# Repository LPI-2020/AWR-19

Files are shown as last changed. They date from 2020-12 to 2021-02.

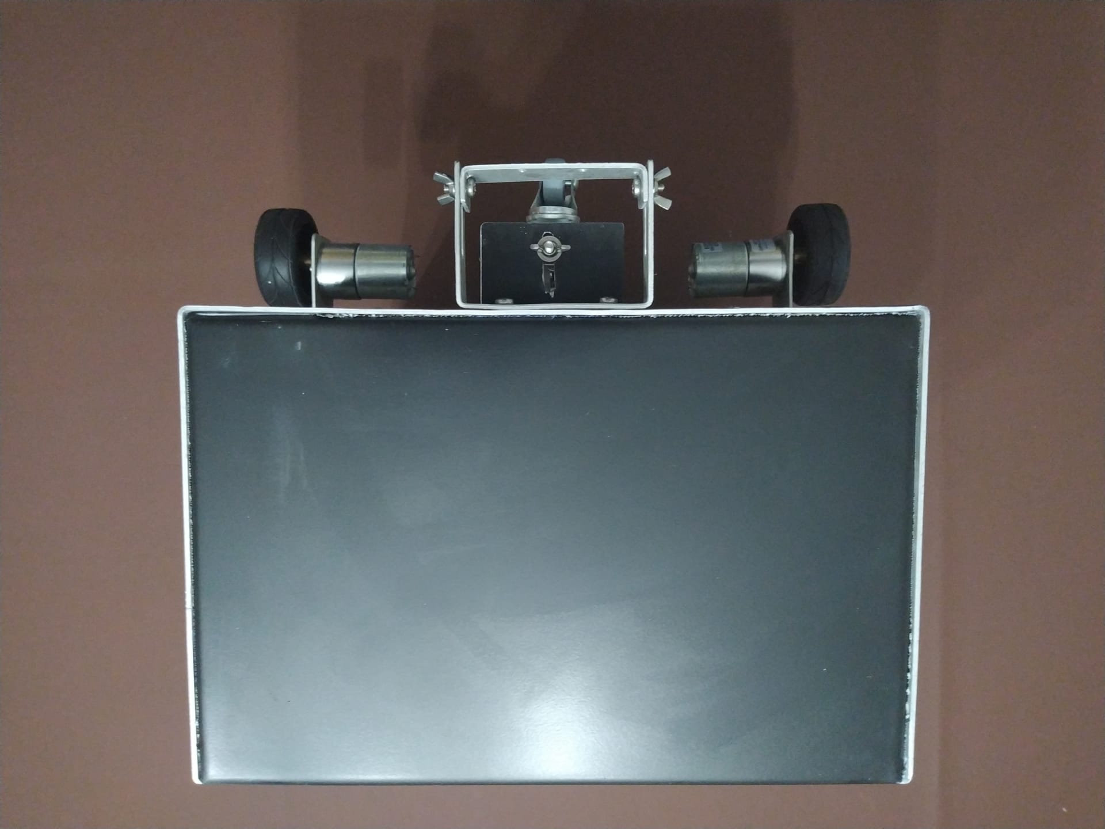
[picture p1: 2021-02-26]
01Relatorios/Images/FotosRobo/frente.jpg

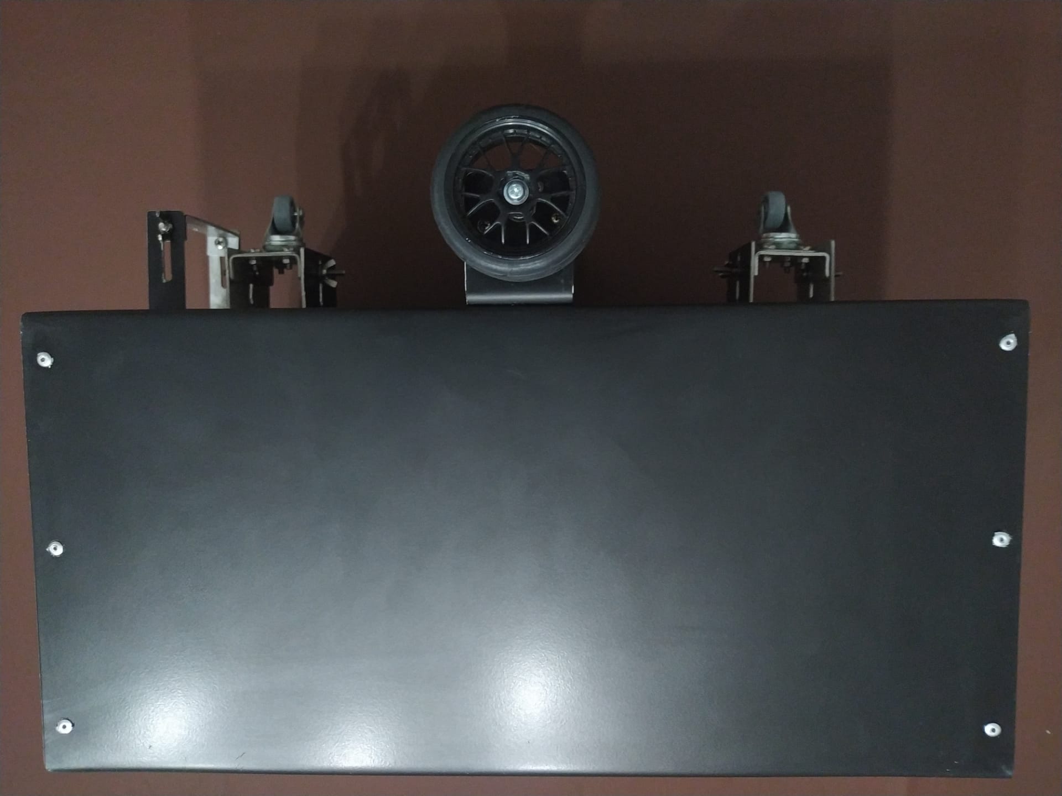
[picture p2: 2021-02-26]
01Relatorios/Images/FotosRobo/lado_esq.jpg

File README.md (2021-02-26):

# Analog Waiter Robot (AWR-19)

Developed in:
- Projeto Integrador - LPI I (2020)

Members:
- Bruno Miguel Vasconcelos da Silva, a88289
- Diogo Miguel Cunha Fernandes, a88262
- Duarte Miguel Novo Rodrigues, a88259
- Francisco Lopes Salgado, a88231 
- João Pedro Dias Miranda, a88237
- José Tomás Lima de Abreu, a88218

Directed by:
- Luís Barros

Short description (PT):
- O Analog Waiter Robot (AWR) é um robô seguidor de linha focado na assistência a pessoas em isolamento que não podem contactar com o mundo exterior. Basta colocar no seu suporte o que pretende fazer chegar ao paciente, colocá-lo sobre a linha, ligá-lo e este seguirá o percurso até ao destino.

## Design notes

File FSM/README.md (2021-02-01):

# PI-LPI_I/FSM

**_Version_ currently in use: v1.8**

Resources - Holds various materials that helped or will help implement features.

v1 - Robot makes 180 degree turn when arriving at the end of the line and then stops.
     After that, whenever the user wants to send back the robot, a button can be pressed to begin movement.

v2 - Robot stops at the end of the line. After that, whenever the user wants to send back the robot,
     a button can be pressed to begin movement in the opposite direction that he came.

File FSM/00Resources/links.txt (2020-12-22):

Driver Motores: https://www.botnroll.com/pt/motores-e-atuadores/1000-l298n-motor-driver-board-.html
Toggle: https://www.allaboutcircuits.com/technical-articles/t-is-for-toggle-understanding-the-t-flip-flop/
Mapa karnough: http://www.32x8.com/var6.html
Debounce: https://www.youtube.com/watch?v=tmjuLtiAsc0

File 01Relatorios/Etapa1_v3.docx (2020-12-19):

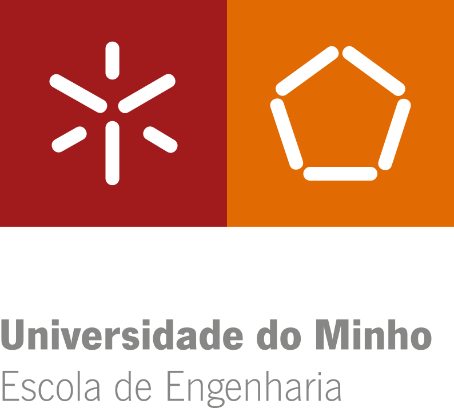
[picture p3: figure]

Bruno Miguel Vasconcelos da Silva, a88289

Diogo Miguel Cunha Fernandes, a88262

Duarte Miguel Novo Rodrigues, a88259

Francisco Lopes Salgado, a88231

João Pedro Dias Miranda, a88237

José Tomás Lima de Abreu, a88218

AWR-19

Analog Waiter Robot

Projeto integrador

Laboratórios e Práticas Integradas

Trabalho realizado sob a orientação do

Professor Luís Barros

dezembro de 2020

Índice

# Lista de Figuras

# Lista de Tabelas

# Acrónimos e Siglas

Acrónimo/Sigla | Significado
AWR LED | Analog Waiter Robot Light emitting diode

# Introdução

## Introdução

Perante o atual panorama pandémico da Covid-19 [1], pretende-se implementar uma ideia que terá um impacto positivo na vida das pessoas infetadas pela doença bem como dos que as rodeiam.

A maioria das ideias nesta área tem como foco principal a saúde pública da população em geral, tais como, robôs de desinfeção, por exemplo. Há menos projetos com foco individual em pessoas que tenham contraído a doença.

Na China existe um robô (little peanut) [2] com a mesma finalidade que foi utilizada num hotel para entregar comida porta a porta a hóspedes com suspeita de infeção.

Tendo em consideração que uma pessoa em isolamento deve evitar o contacto com o mundo exterior, pretende-se desenvolver um produto que permita a entrega e recolha de bens essenciais de forma segura. De forma a facilitar a sua desinfeção e o seu manuseamento, o robô deverá ter superfícies lisas e uma interface simples.

## Enquadramento

O Analog Waiter Robot (AWR) é um robô seguidor de linha focado na assistência a pessoas em isolamento que não podem contactar com o mundo exterior. Basta colocar no seu suporte o que pretende fazer chegar ao paciente, colocá-lo sobre a linha, ligá-lo e este seguirá o percurso até ao destino.

## Especificações previstas

O AWR terá de deslocar-se entre dois pontos, previamente definidos, com base numa linha instalada nos meios de acesso à divisão em que o paciente em questão se situa.

O AWR terá de ser colocado sobre a linha com os bens essenciais (comida e/ou alimentos) num tabuleiro. Após estar alinhado, deverá ser ligado por um funcionário responsável, para que inicie a sua trajetória. Ao chegar ao destino, demarcado com uma cruz no fim da linha, o robô terá de parar de forma a que o paciente recolha os bens a si destinados. Quando o paciente desejar, poderá acionar o robô de forma a que este reinicie o seguimento da linha de volta ao ponto de partida. Para tal, o AWR fará uma rotação de 180 ° sobre a linha e iniciar a marcha até ao ponto de início. Como a alimentação do robô será a baterias, eventualmente, terá de ser ligado à rede elétrica para ser carregado.

O tipo de desenvolvimento do nosso produto pode ser classificado como “misto”, uma vez que não tem necessariamente características inovadoras, mas é concebido para servir as necessidades particulares de um comprador. O produto será composto na sua totalidade por componentes ou subsistemas que são comprados “off-the-shelf”. Isto é, que só precisam de ser instalados e configurados para entrarem em funcionamento.

## Testes previstos

De forma a testar as especificações acima previstas, deverão ser realizados testes.

Para que o AWR siga a linha, será implementado um seguidor de linha através de um array de sensores de reflexão de luz. Irão ser realizados ensaios experimentais simulando o ambiente no qual este irá operar. Estes permitirão determinar os valores de referência que servirão para o dimensionamento e calibração dos circuitos de direção do robô. Para isso, este deverá ser colocado em diferentes posições sobre a linha.

Depois de determinados os valores de referência, deverão ser testados os circuitos de direção do robô, que usarão controladores para manter os valores dos sensores na gama de referência. Para isso, o AWR deverá ser colocado em diferentes posições sobre a linha para verificar se o controlador cumpre o seu propósito. Isto é, se o robô segue a linha até ao destino final.

Para controlar os diferentes estados de funcionamento do robô, irá ser desenvolvida uma máquina de estados baseada em circuitos sequenciais. De forma a testar o seu funcionamento, esta deverá ser sujeita a diferentes inputs de forma a verificar a comutação entre estados com a utilização de LEDs nas suas saídas. As saídas da máquina de estados irão controlar o estado de funcionamento dos motores.

Consoante as saídas da máquina de estados, cada motor poderá ter três modos de funcionamento: sentido horário, sentido anti-horário ou parado. Nesse momento poderão ser testadas todas as funcionalidades do robô, verificando se segue a linha ou não.

## Planeamento inicial

De forma a testar as especificações acima previstas, deverão ser realizados testes.

Para que o AWR siga a linha, será implementado um seguidor de linha através de um array de sensores de reflexão de luz. Irão ser realizados ensaios experimentais simulando o ambiente no qual este irá operar. Estes permitirão determinar os valores de referência que servirão para o dimensionamento e calibração dos circuitos de direção do robô. Para isso, este deverá ser colocado em diferentes posições sobre a linha.

Depois de determinados os valores de referência, deverão ser testados os circuitos de direção do robô, que usarão controladores para manter os valores dos sensores na gama de referência. Para isso, o AWR deverá ser colocado em diferentes posições sobre a linha para verificar se o controlador cumpre o seu propósito. Isto é, se o robô segue a linha até ao destino final.

Para controlar os diferentes estados de funcionamento do robô, irá ser desenvolvida uma máquina de estados baseada em circuitos sequenciais. De forma a testar o seu funcionamento, esta deverá ser sujeita a diferentes inputs de forma a verificar a comutação entre estados com a utilização de LEDs nas suas saídas. As saídas da máquina de estados irão controlar o estado de funcionamento dos motores.

Consoante as saídas da máquina de estados, cada motor poderá ter três modos de funcionamento: sentido horário, sentido anti-horário ou parado. Nesse momento poderão ser testadas todas as funcionalidades do robô, verificando se segue a linha ou não.

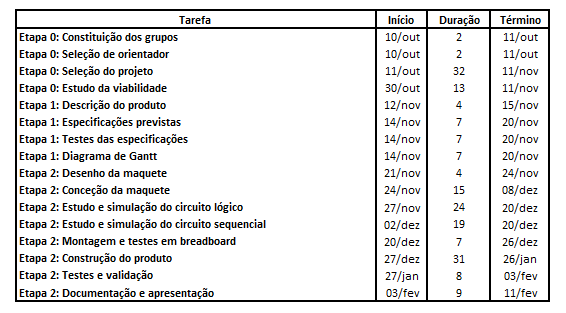
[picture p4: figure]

Tabela 1 - Planeamento do Projeto

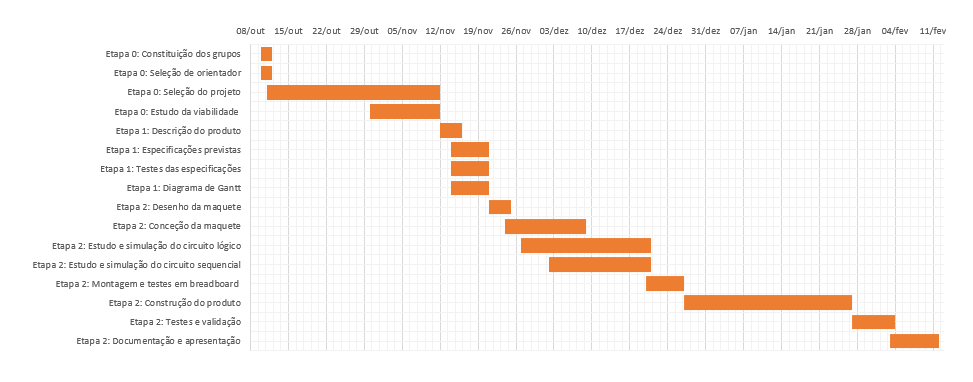
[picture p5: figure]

Figura 1 - Diagrama de Gantt

# Referências

[1] SNS - Serviço Nacional de Saúde, “Covid-19 | Pandemia,” 11 março 2020. [Online]. Available: https://www.sns.gov.pt/noticias/2020/03/11/covid-19-pandemia/. [Acedido em 16 dezembro 2020].

[2] J. D'Onfro, “Robots To The Rescue: How High-Tech Machines Are Being Used To Contain The Wuhan Coronavirus,” 2 fevereiro 2020. [Online]. Available: https://www.forbes.com/sites/jilliandonfro/2020/02/02/robots-to-the-rescue-how-high-tech-machines-are-being-used-to-contain-the-wuhan-coronavirus/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. [Acedido em 16 dezembro 2020].

LPI I | Projeto Integrador | AWR-19 xv Universidade do Minho

Lista de Figuras

Lista de Tabelas

Acrónimos e Siglas

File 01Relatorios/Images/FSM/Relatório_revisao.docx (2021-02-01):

3.3 - Sistema eletrónico para o controlo dos motores (pcbs e ligações)

De forma a ser possível controlar o estado de funcionamento do robô, ou seja, fazê-lo seguir a linha, parar ou rodar 180 °, desenvolveu-se uma máquina de estados sequencial síncrona, mais especificamente uma máquina de Moore, uma vez que as suas saídas dependem apenas do estado atual.

Figura 1 - Máquina de Moore

Numa máquina de estados, o objetivo é determinar a “Lógica do Próximo Estado” e a “Lógica de Saída” do circuito. Como referido, a “Lógica de saída” depende apenas do estado atual. Já a “Lógica do Próximo Estado” depende do estado atual e das entradas do circuito.

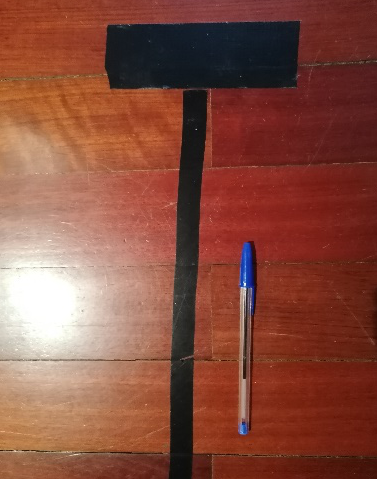
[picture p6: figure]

Como referido, o objetivo do robô é seguir uma linha, devendo parar sobre uma linha horizontal colocada no final do percurso (Figura 2) e, nesse momento, o robô deve dar uma volta de 180 ° sobre o seu eixo, voltando a seguir a linha em direção ao ponto de partida, após o acionamento de um botão.

Figura 2 - Linha preta usada para os testes

Denominou-se a linha de final de curso como a linha horizontal e a linha determinante do percurso como linha vertical.

De modo a detetar a linha no final do percurso, usaram-se os dois sensores das pontas do array de sensores (S1 e S8, rodeados a amarelo na Figura 4). Usou-se também o sensor do meio (S5, rodeado a verde na Figura 4) de forma a interromper a rotação quando este encontrar a linha preta.

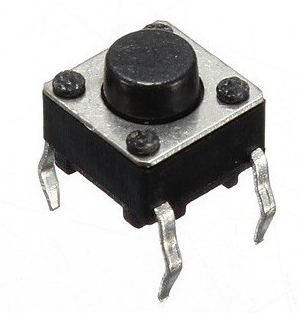
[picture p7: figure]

Nesse momento, o robô poderá ser acionado através de um botão de pressão (B) (Figura 3) para que este volte a seguir a linha.

Figura 3 - Botão de Pressão

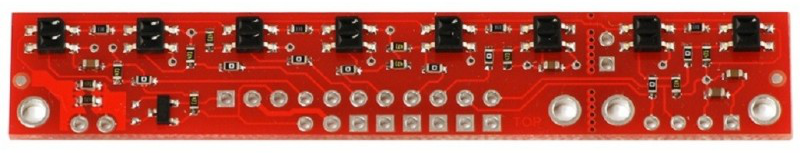
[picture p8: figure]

Figura 4 – Sensores usados na máquina de estados: S1, S5 e S8

Os motores são controlados por meio de um driver (L298N), podendo estar parados, a rodar no sentido horário ou no sentido anti-horário. O driver possui quatro entradas, duas por cada motor.

Para isso, na máquina de estados existem duas saídas por cada motor, sendo que uma controla o movimento no sentido horário e outra no sentido anti-horário.

Como o robô usa dois motores, existem quatro saídas, que quando estão ativas (nível lógico alto) despoletam as seguintes respostas:

- FWR – motor da direita roda no sentido horário;
- FWL – motor da esquerda roda no sentido horário;
- BWR – motor da direita roda no sentido anti-horário;
- BWL – motor da esquerda roda no sentido anti-horário.

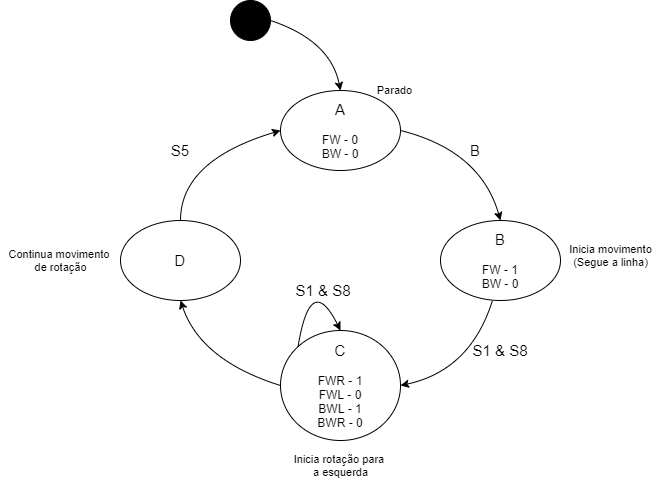
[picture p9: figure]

Na figura seguinte, mostra-se o diagrama da máquina de estados, usada para controlar o modo de funcionamento do robô. FW representa os valores de FWR e FWL e BW representa os valores de BWR e BWL.

Figura 5 - Diagrama da Máquina de Estados

Inicialmente, no estado “A”, o robô está parado (FW = 0 e BW = 0), e espera pelo acionamento do botão para iniciar a marcha. Após o acionamento do botão, B a nível lógico alto, no estado “B”, o robô inicia a sua trajetória, seguindo a linha com os dois motores a rodar no sentido horário (FW = 1 e BW = 0). Quando o array de sensores estiver posicionado sobre a linha horizontal preta (fim do trajeto), os sensores S1 e S8 estarão a nível lógico alto, e ocorrerá a transição para o estado “C”. Neste estado, o robô inicia a rotação para a esquerda (FWR = 1, FWL = 0, BWR = 0 e BWL = 1) e não transita de estado enquanto os sensores S1 e S8 estiverem a nível lógico alto, isto é, enquanto o array de sensores estiver sobre a linha horizontal. Quando o array de sensores sair desta, S1 e S8 estarão a nível lógico baixo, avançando para o estado “D”, no qual o robô continua a rotação, mantendo as suas saídas, até que o sensor S5 esteja sobre a linha vertical, S5 a nível lógico alto. Assim posicionado, o robô volta ao estado inicial.

Tabela 1 - Tabela Completa para Determinação da Lógica Completa da Máquina de Estados

De forma a implementar a máquina de estados, de acordo com o diagrama de estados, determinou-se toda a lógica necessária, construindo a tabela 1.

Adicionaram-se duas colunas que indicam os bits do estado atual (B1 e B0) e também as entradas da máquina de estados (S1, S5, S8 e B). Como existem quatro entradas, existem dezasseis (2⁴) combinações possíveis para cada estado, o que resulta em sessenta e quatro possibilidades no total (2⁴⁺² = 2⁶ = 64) que será o número de linhas da tabela 1.

A seguir, “E” representa o estado atual e “E*” o estado seguinte. “B1*” e “B0*” representam os bits do estado seguinte. Estas colunas devem ser preenchidas de acordo com a tabela ao lado (Tabela 2).

Tabela 2 - Atribuição de Estados

Sabendo que cada flip-flop permite a existência de dois estados e que existem quatro estados (A – D), selecionaram-se dois flip-flops do tipo J-K, que apresentam a tabela de excitação ao lado (Tabela 3). De acordo com esta tabela, foram preenchidas as colunas “J” e “K” para cada flip-flop (Ja e Ka, relativo a B0; Jb e Kb, relativo a B1). Para este efeito, determinou-se a lógica do próximo estado, em função das quatro entradas da máquina de estados, simplificada através de mapas de Karnaugh. Resolveram-se quatro mapas de Karnaugh (um para cada entrada J e K dos flip-flops) e obteve-se os resultados apresentados na figura 6.

Tabela 3 - Tabela de Excitação do Flip-Flop JK

Figura 6 - Lógica do Próximo Estado

Adicionaram-se as colunas das saídas (FWR, FWL, BWR e BWL), as quais foram preenchidas de acordo com o estado atual. Para cada uma destas determinou-se a lógica de saída, que também foi simplificada através de mapas de Karnaugh. Os resultados obtidos foram os da figura 7.

Figura 7 - Lógica de Saída

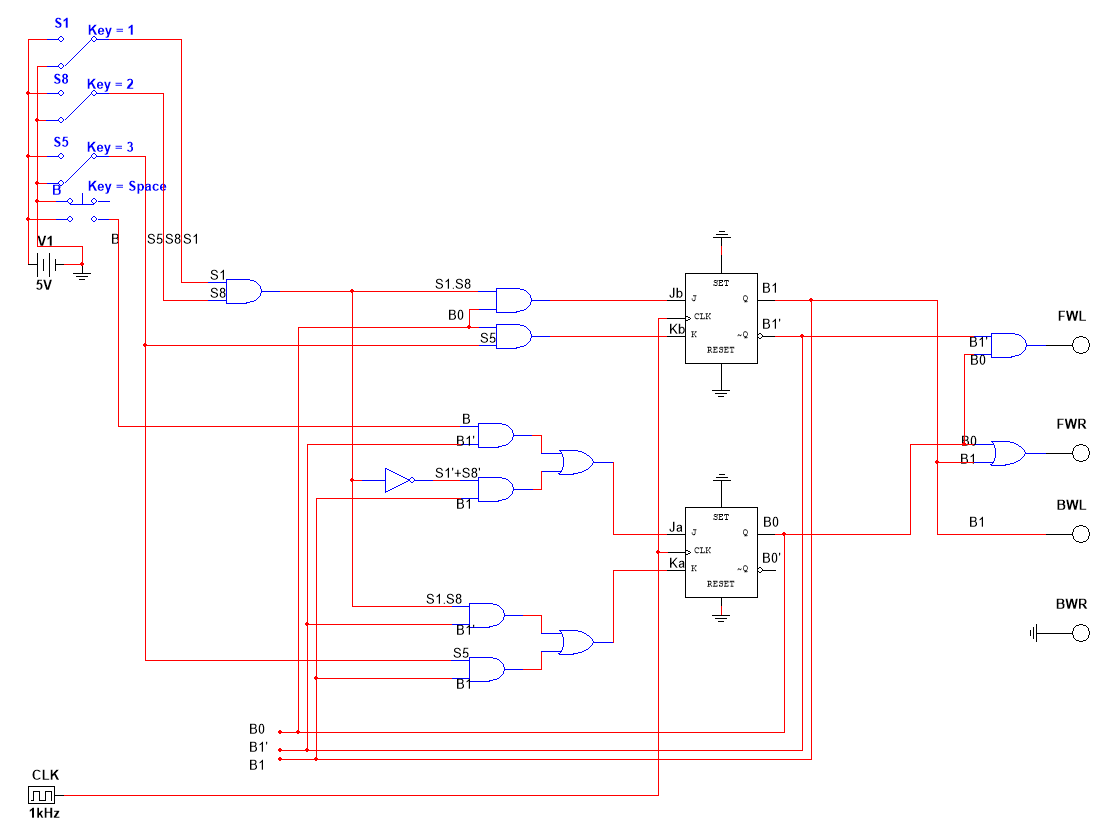
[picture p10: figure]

De acordo com a lógica determinada, desenhou-se o circuito que implementa a máquina de estados, o qual foi testado usando a ferramenta Multi-Sim, verificando-se a sua funcionalidade.

Lógica de próximo estado

Entradas

Figura 8 - Desenho da Máquina de Estados

Lógica de saída

Saídas

Flip-Flops

Estado atual

Lógica de Entrada

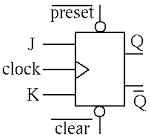
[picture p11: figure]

Tal como mostra a figura 9, cada Flip-Flop J-K necessita de um sinal clock como entrada. O clock é um sinal em forma de onda quadrada com um duty-cycle de, idealmente, 50 %. Dá-se uma transição entre estados sempre que, a cada pulso de clock, uma das entradas (J ou K) estiver a nível lógico alto.

Figura 9 - Esquema do Flip-Flop J-K

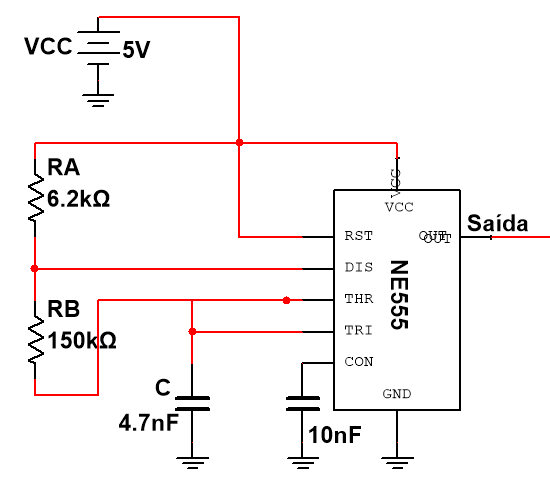
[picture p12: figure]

Para este efeito, implementou-se um oscilador usando o integrado NE555 numa montagem como multivibrador astável.

Figura 10 - Implementação do Oscilador

O condensador C1 carrega até 2*VCC/3 através das resistências RA e RB (saída = 1). Quando C1 atinge este valor, irá descarregar por RB (saída=0), até uma tensão de VCC/3 e o ciclo repete-se.

Para este efeito, implementou-se um oscilador usando o integrado NE555 numa montagem como multivibrador astável.

O condensador C1 carrega até 2*VCC/3 através das resistências RA e RB (saída = 1). Quando C1 atinge este valor, irá descarregar por RB (saída=0), até uma tensão de VCC/3 e o ciclo repete-se.

Através dos seguintes cálculos, dimensionaram-se os componentes para obter uma onda quadrada de frequência 1 kHz, duty-cycle de 50 %, aproximadamente.

T_(ON) =0,693 (RA+RB) C T_(OFF) =0,693 (RB) C

Duty-cyle=50 % ⇔T_(ON) = T_(OFF)

T= T_(ON) + T_(OFF) ⇔T=0,693 (R_A +2R_B ) C ⇔f= 1/T ⇔ f=(1,44)/((R_A +2R_B ) C) Para f=1 kHz e C=4,7 ηF :

(R_A + 2R_B )=306383

Duty-cyle=1- (R_B)/(R_A + 2R_B) ⇔R_B =0,5 (R_A + 2R_B ) ⇔R_B =0,5 ×306383 ⇔R_B =153,2 kΩ

(R_A + 2R_B )=306383

⇔R_A =6,4 kΩ

Foram selecionados os valores standard das resistências (Série E24) e do condensador (Série E12) mais próximos dos obtidos:

R_A =6,2 kΩ R_B =150 kΩ C=4,7 ηF

A figura 11 mostra a saída do circuito obtida em simulação com a ferramenta TINA.

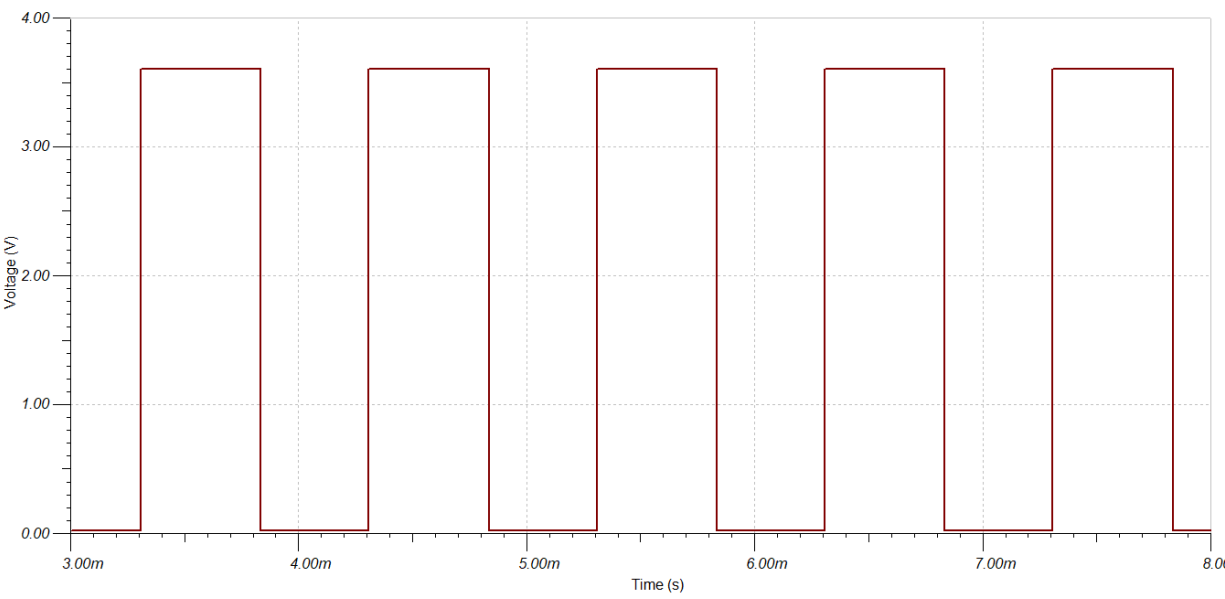
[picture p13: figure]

Figura 11 - Resposta do Oscilador de 1 kHz

As entradas Clear dos Flip-Flops J-K utilizados são ativas a nível lógico baixo, isto é, se ligarmos esta entrada ao ground, ocorrerá um reset no flip-flop e sua a saída Q virá a nível lógico baixo, independentemente das suas entradas J e K. Assim, se na máquina de estados as entradas Clear forem ligadas ao GND, B0 e B1 ficarão a nível lógico baixo.

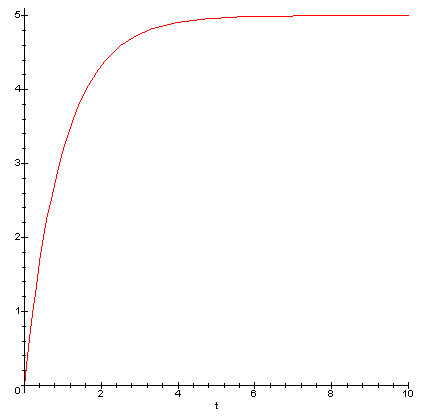
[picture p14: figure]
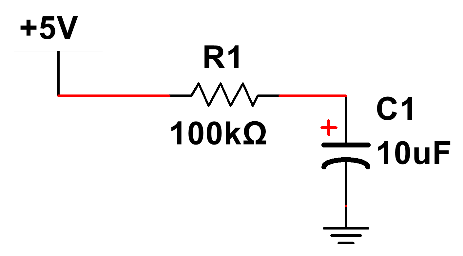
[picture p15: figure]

Experimentalmente, verificou-se que, quando alimentados, os flip-flops mantêm as saídas do estado anterior. Para que o robô inicie no primeiro estado de funcionamento (estado “A”), utilizou-se um circuito para efetuar um reset aos flip-flops, tal como mostra a figura 10.

Figura 12 - Circuito RC de Reset e a sua resposta no tempo.

Sabendo que a saída deste circuito estará a nível lógico baixo enquanto o condensador não carregar, a entrada reset dos flip-flops estará também a nível lógico baixo, o que resulta na ação de reset. Assim, logo que se alimentar a máquina de estados, os flip-flops apresentarão nas saídas “Q” o nível lógico baixo que representa o primeiro estado de funcionamento do robô. Após o condensador carregar, a entrada reset estará a nível lógico alto durante o resto do tempo de funcionamento, não provocando um reset indesejado.

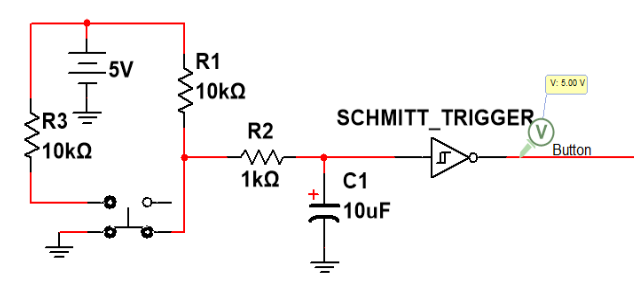
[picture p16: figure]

Foi usado um botão de pressão para que o robô inicie a marcha. No entanto, sabe-se que, quando uma saída provém diretamente de um botão de pressão, esta é afetada por problemas de vibração mecânica (bounce) quando o contacto se fecha. De forma a garantir que a mudança de nível lógico se faça sem oscilações, torna-se necessário implementar um circuito de debounce como, por exemplo, o apresentado na figura 13.

Figura 13 - Circuito de Debounce do Botão de Pressão (quando premido)

O condensador em conjunto com a resistência funciona como filtro passa-baixo, que ajuda a reduzir o ruído elétrico provocado pelas vibrações mecânicas do botão. Assim, quando o botão não está pressionado, os terminais do condensador apresentarão 5 V e, quando pressionado, apresentarão 0 V. Uma vez que, num circuito sequencial, o nível lógico alto corresponde ao acionamento de uma entrada (botão, neste caso), será necessário utilizar uma lógica inversora na saída do condensado. Para isso, usou-se uma porta lógica Schmitt-Trigger (integrado 74HCT14) que funciona como um circuito comparador inversor com histerese centrado em 0 V. Assim, aumenta a imunidade ao ruído e, como inverte, a saída do circuito estará a nível lógico alto quando o botão for pressionado.

Foi feito o teste em simulação do circuito da máquina de estados através da ferramenta Multi-Sim. Os resultados obtidos apresentam-se nas figuras abaixo. Verificou-se, portanto, a boa funcionalidade do circuito dimensionado.

Figura 14 - Estado 0 (Parado)

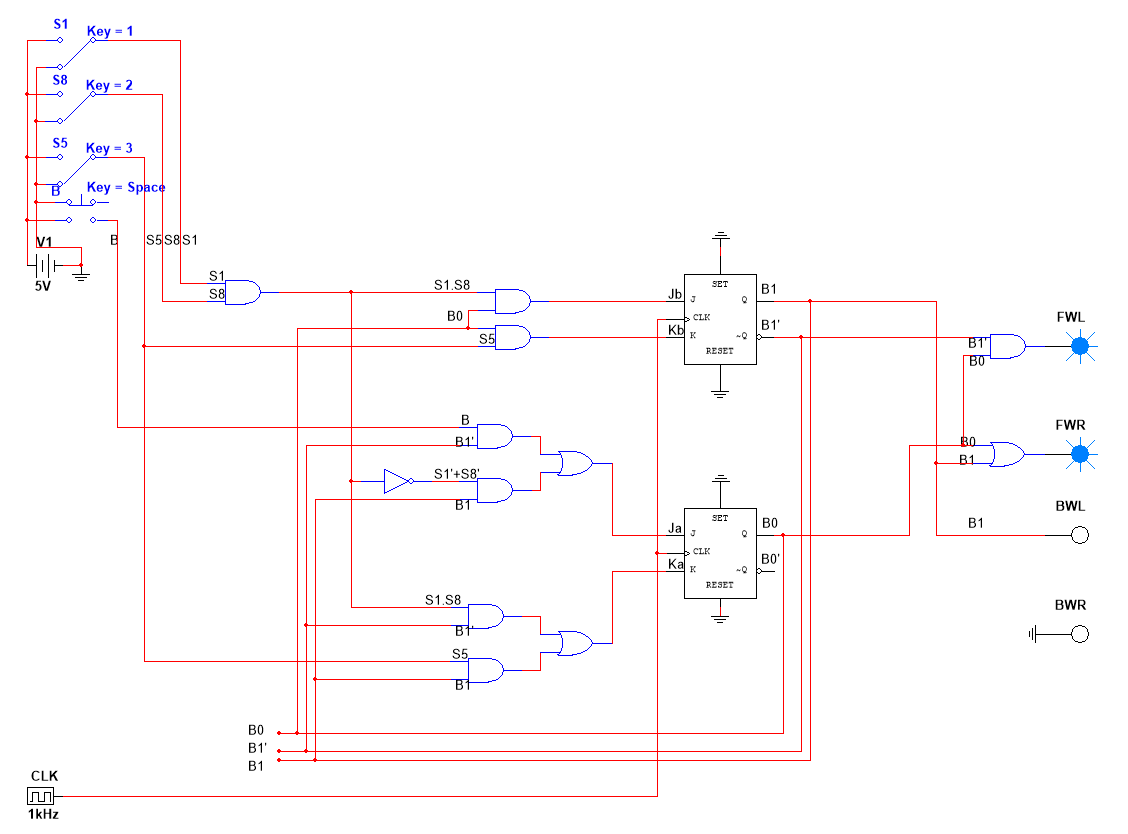
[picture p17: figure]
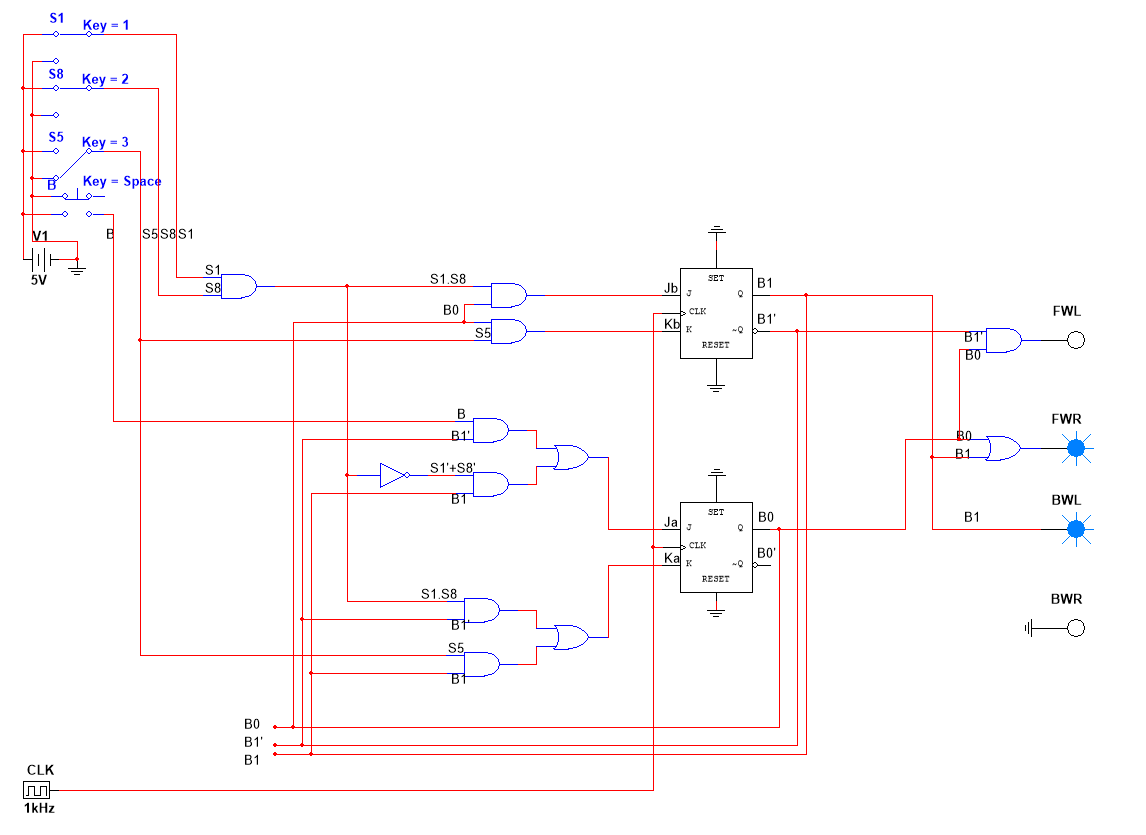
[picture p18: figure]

Figura 16 - Estado 1 (Anda para a frente) – Botão foi pressionado

Figura 15 - Estado 2 (Dá a volta para a esquerda) – S1 e S8 a nível lógico alto

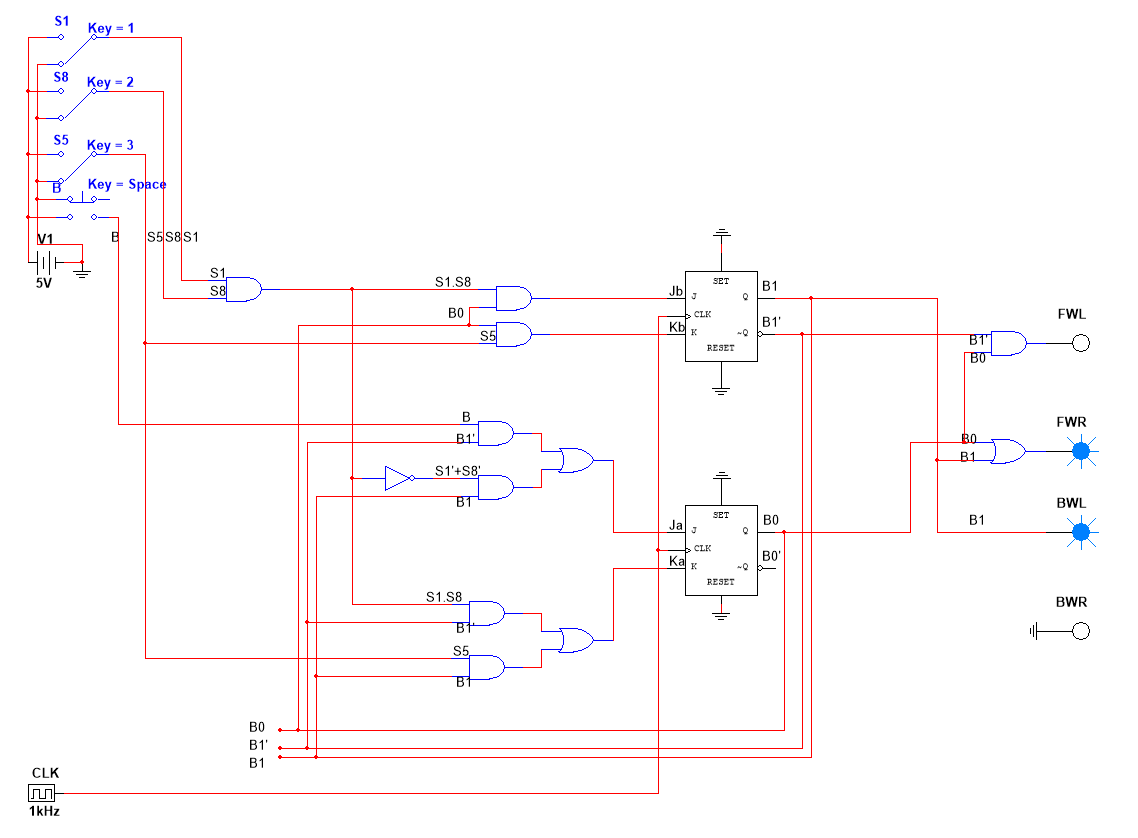
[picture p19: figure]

Figura 17 - Estado 3 (Dá a volta) - S1 e S8 a nível lógico baixo

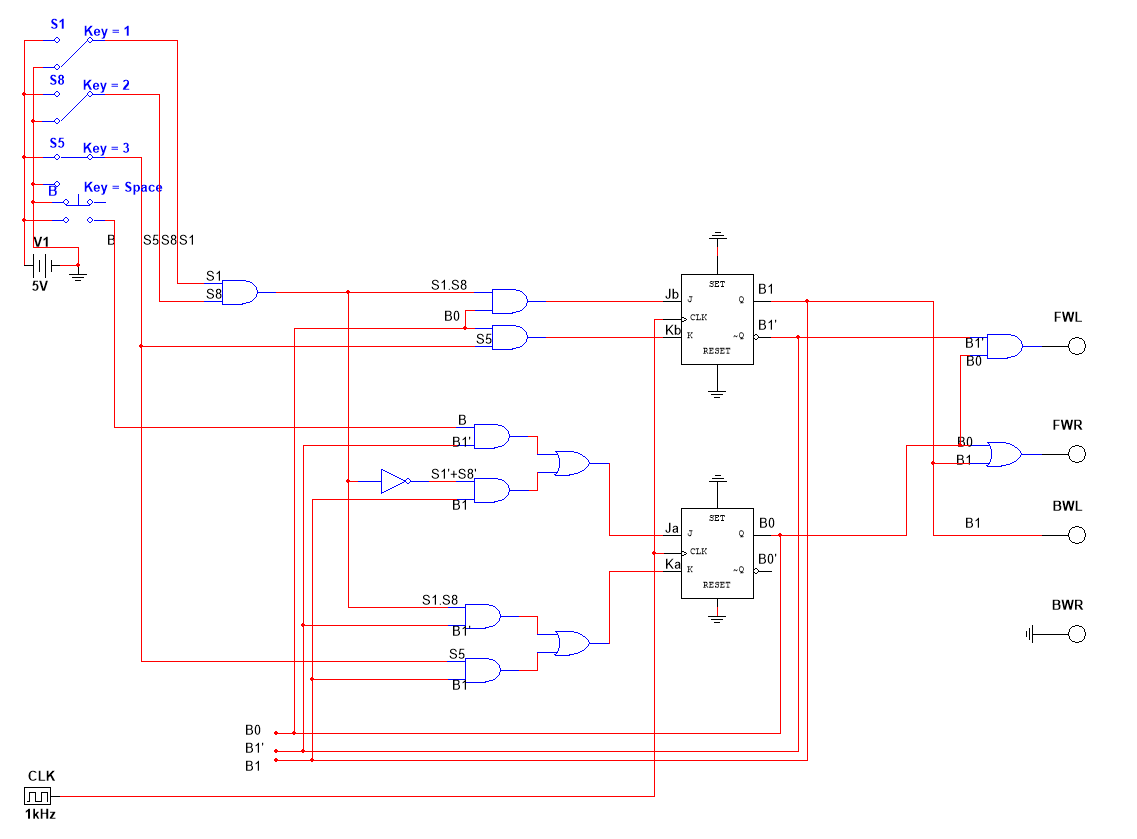
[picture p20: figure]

Figura 18 - Estado 0 (Parado novamente) - S5 = 1

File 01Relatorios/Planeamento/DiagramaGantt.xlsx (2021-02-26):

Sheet: 1a Versao
Tarefa | Início | Duração | Término
Etapa 0: Constituição dos grupos | 2020-10-10 | 2 | 2020-10-11
Etapa 0: Seleção de orientador | 2020-10-10 | 2 | 2020-10-11
Etapa 0: Seleção do projeto | 2020-10-11 | 32 | 2020-11-11
Etapa 0: Estudo da viabilidade | 2020-10-30 | 13 | 2020-11-11
Etapa 1: Descrição do produto | 2020-11-12 | 4 | 2020-11-15
Etapa 1: Especificações previstas | 2020-11-14 | 7 | 2020-11-20
Etapa 1: Testes das especificações | 2020-11-14 | 7 | 2020-11-20
Etapa 1: Diagrama de Gantt | 2020-11-14 | 7 | 2020-11-20
Etapa 2: Desenho da maquete | 2020-11-21 | 4 | 2020-11-24
Etapa 2: Conceção da maquete | 2020-11-24 | 15 | 2020-12-08
Etapa 2: Estudo e simulação do circuito lógico | 2020-11-27 | 24 | 2020-12-20
Etapa 2: Estudo e simulação do circuito sequencial | 2020-12-02 | 19 | 2020-12-20
Etapa 2: Montagem e testes em breadboard | 2020-12-20 | 7 | 2020-12-26
Etapa 2: Construção do produto | 2020-12-27 | 31 | 2021-01-26
Etapa 2: Testes e validação | 2021-01-27 | 8 | 2021-02-03
Etapa 2: Documentação e apresentação | 2021-02-03 | 9 | 2021-02-11

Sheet: 2a Versao
Tarefa | Início | Duração | Término
Etapa 0: Constituição dos grupos | 2020-10-10 | 1 | 2020-10-11
Etapa 0: Seleção de orientador | 2020-10-10 | 1 | 2020-10-11
Etapa 0: Seleção do projeto | 2020-10-11 | 31 | 2020-11-11
Etapa 0: Estudo da viabilidade | 2020-10-30 | 12 | 2020-11-11
Etapa 1: Descrição do produto | 2020-11-12 | 3 | 2020-11-15
Etapa 1: Especificações previstas | 2020-11-14 | 6 | 2020-11-20
Etapa 1: Testes das especificações | 2020-11-14 | 6 | 2020-11-20
Etapa 1: Diagrama de Gantt | 2020-11-14 | 6 | 2020-11-20
Etapa 2: Desenho da maquete | 2020-11-21 | 3 | 2020-11-24
Etapa 2: Conceção da maquete | 2020-11-24 | 14 | 2020-12-08
Etapa 2: Estudo e simulação do circuito lógico | 2020-11-27 | 23 | 2020-12-20
Etapa 2: Estudo e simulação do circuito sequencial | 2020-12-02 | 18 | 2020-12-20
Etapa 2: Montagem e testes em breadboard | 2020-12-20 | 33 | 2021-01-22
Etapa 2: Estudo de Fiabilidade, Certifiação e Segurança | 2021-01-23 | 18 | 2021-02-10
Etapa 2: Documentação e apresentação | 2021-01-23 | 19 | 2021-02-11

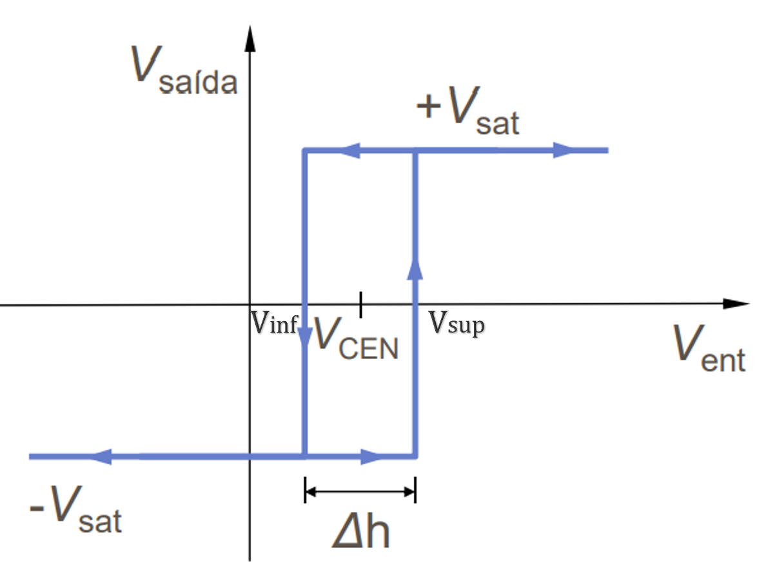
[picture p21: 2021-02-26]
01Relatorios/Images/histerese.png

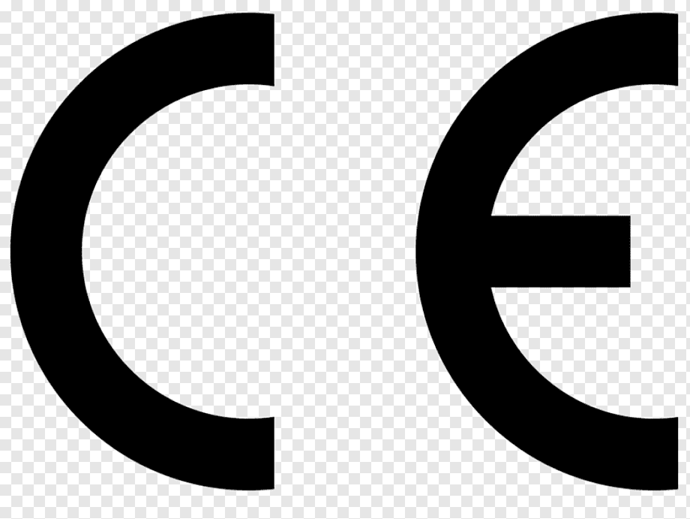
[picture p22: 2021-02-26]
01Relatorios/Images/Simbolos/ce.jpeg

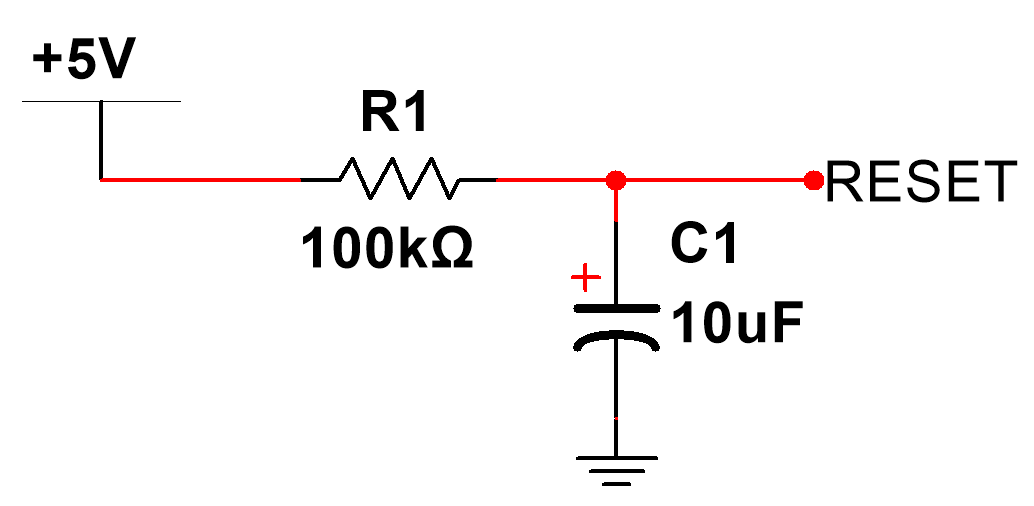
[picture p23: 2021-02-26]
01Relatorios/Images/FSM/circuitoRC.png

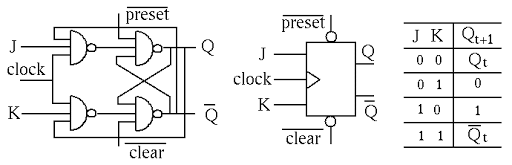
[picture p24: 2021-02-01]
01Relatorios/Images/FSM/FlipFlop_JK.png

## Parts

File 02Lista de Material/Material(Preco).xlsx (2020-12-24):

Material | Quantidade | Preço (€) (c/iva)
Motor Bot'n Roll ONE 300rpm | 2 | 35.001
Par de rodas Bot'n Roll ONE A | 1 | 11.500
Conjunto de Hubs para eixos 4mm c/exterior sextavado 12mm | 1 | 4.945
Rodas Livres | 2 | 3.000
Placa driver de motores L298N | 1 | 9.102
Suporte para uma pilha 18650 c/fios | 3 | 2.550
BMS para proteção Baterias 18650 3S 12,6V 20A | 1 | 3.948
Sensor QTR8A | 1 | 15
Circuitos Integrados | 10 | 10
Placa Impressa | 1
Acrilico | 1 | 0
Aluminio | 1 | 0
 |  | 95.046 | Total

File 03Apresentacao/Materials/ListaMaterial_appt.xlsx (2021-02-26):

 | Material | Quantidade | Preço unitário | Preço total
1 | Motores | 2 | 17.50 € | 35.00 €
2 | Rodas | 1 | 11.50 € | 11.50 €
3 | Par de hubs | 1 | 4.50 € | 4.50 €
4 | Rodas livres | 2 | 1.69 € | 3.38 €
5 | Módulo driver L298N | 1 | 12.90 € | 12.90 €
6 | QTR-8A | 1 | 19.90 € | 19.90 €
7 | Suporte pilha 18650 | 6 | 0.85 € | 5.10 €
8 | BMS | 2 | 5.50 € | 11.00 €
9 | Pilha LI-ION 18650 | 6 | 3.90 € | 23.40 €
10 | LM7805 | 1 | 0.50 € | 0.50 €
11 | TL494 | 2 | 1.70 € | 3.40 €
12 | LM324 | 2 | 1.95 € | 3.90 €
13 | LM358 | 5 | 0.74 € | 3.70 €
14 | 74HCT04 | 1 | 0.92 € | 0.92 €
15 | 74HCT08 | 2 | 0.90 € | 1.80 €
16 | 74HCT14 | 1 | 0.61 € | 0.61 €
17 | 74HCT32 | 1 | 0.48 € | 0.48 €
18 | 74HCT112 | 1 | 1.32 € | 1.32 €
19 | NE555P | 1 | 0.32 € | 0.32 €
20 | Terminal 2 pinos | 17 | 0.80 € | 13.60 €
21 | Terminal 3 pinos | 1 | 1.00 € | 1.00 €
22 | Potenciómetro | 2 | 2.20 € | 4.40 €
23 | Resistência | 34 | 0.05 € | 1.70 €
24 | Condensador cerâmico | 28 | 0.10 € | 2.80 €
25 | Condensador eletrolítico | 4 | 0.25 € | 1.00 €
26 | Botão de pressão | 2 | 0.15 € | 0.30 €
27 | Botão de painel | 1 | 0.60 € | 0.60 €
28 | Terminal 12 conetores | 3 | 0.40 € | 1.20 €
29 | Alumínio 2 mm | - | - | 35.00 €
30 | Placa madeira | 1 | - | 5.00 €
31 | Placa de acrílico policarbonato | 1 | - | 10.00 €
32 | Parafuso 5 mm | 28 | 0.05 € | 1.40 €
33 | Parafuso 3 mm | 12 | 0.05 € | 0.60 €
34 | Porca com asas 5 mm | 6 | 0.10 € | 0.60 €
35 | Porca 5 mm | 22 | 0.05 € | 1.10 €
36 | Rebites | 18 | 0.10 € | 1.80 €
37 | Anilhas | 12 | 0.01 € | 0.12 €
38 | Jumpers | pack | 2.00 € | 2.00 €
Total |  |  |  | 227.85 €

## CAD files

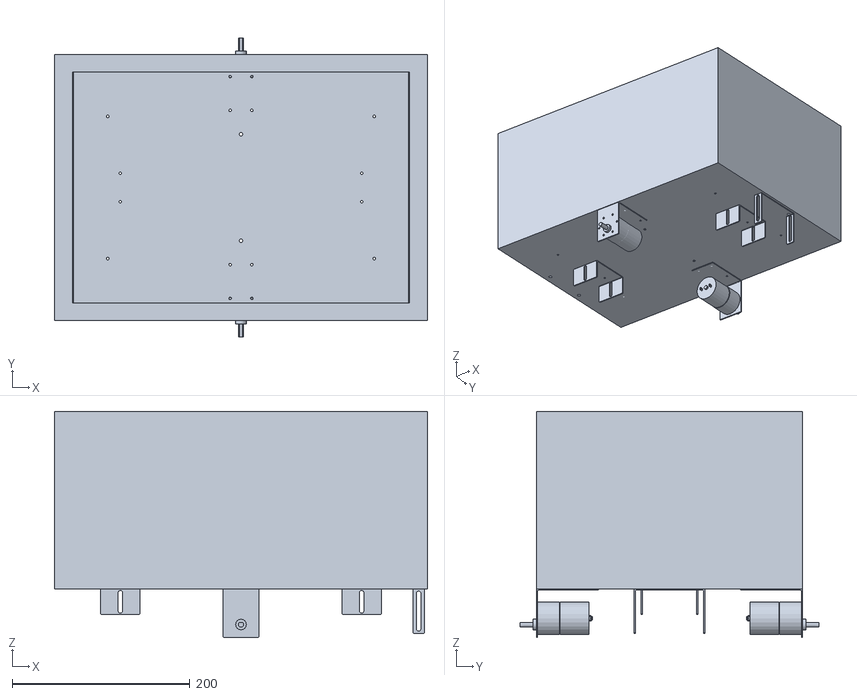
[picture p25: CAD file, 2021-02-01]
Diagramas/Model Robo v2.stl
420.0 x 337.0 x 255.0

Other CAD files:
Diagramas/Diagrama_Robo_v2.dwg

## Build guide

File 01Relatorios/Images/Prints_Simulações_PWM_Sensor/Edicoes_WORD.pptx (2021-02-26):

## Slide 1

1º Estágio

3º Estágio

4º Estágio

5º Estágio

2º Estágio

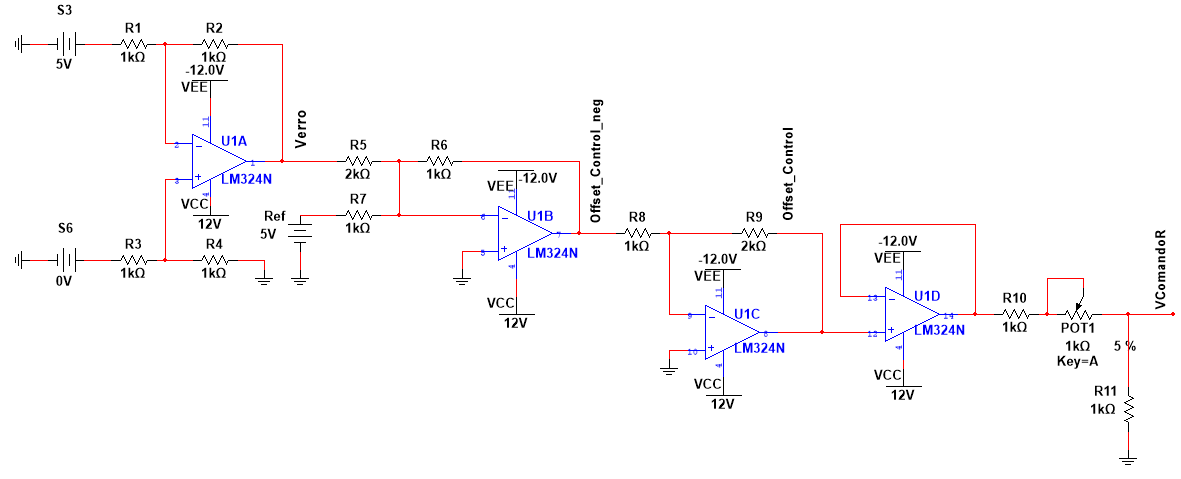
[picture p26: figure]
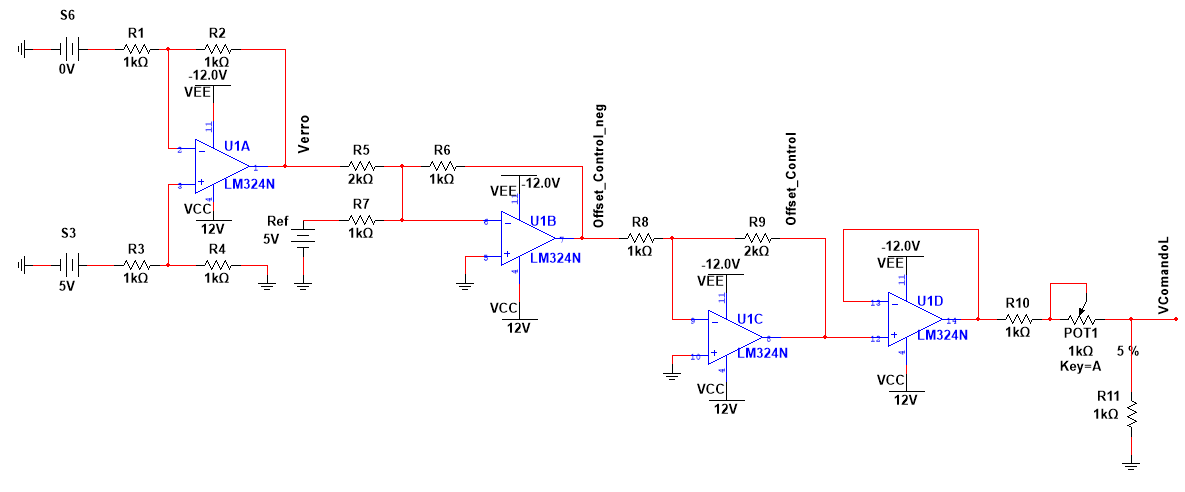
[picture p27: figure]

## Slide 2

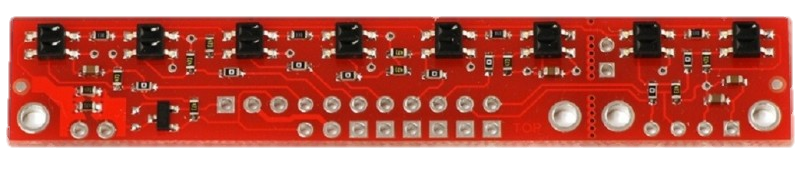
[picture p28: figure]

Sensor 1

Sensor 2

Sensor 3

Sensor 4

Sensor 5

Sensor 6

Sensor 7

Sensor 8

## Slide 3

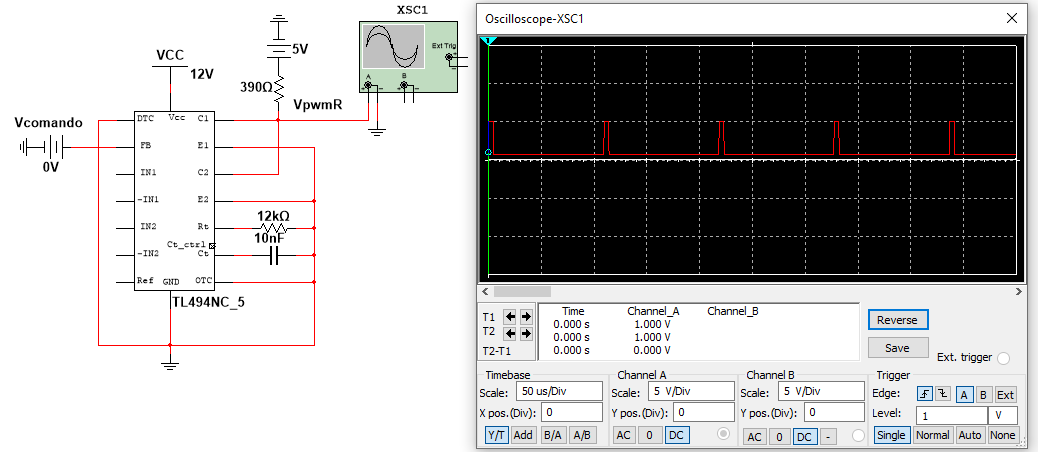
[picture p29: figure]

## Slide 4

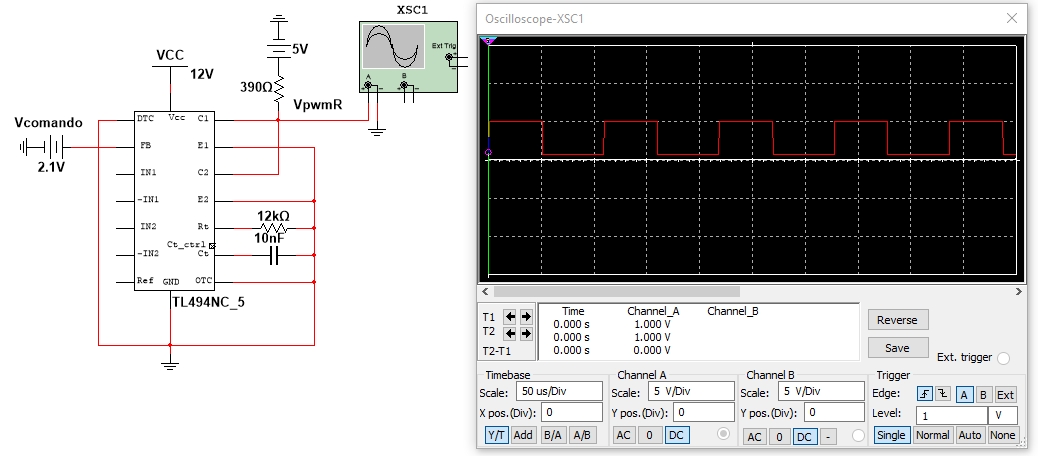
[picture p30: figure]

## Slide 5

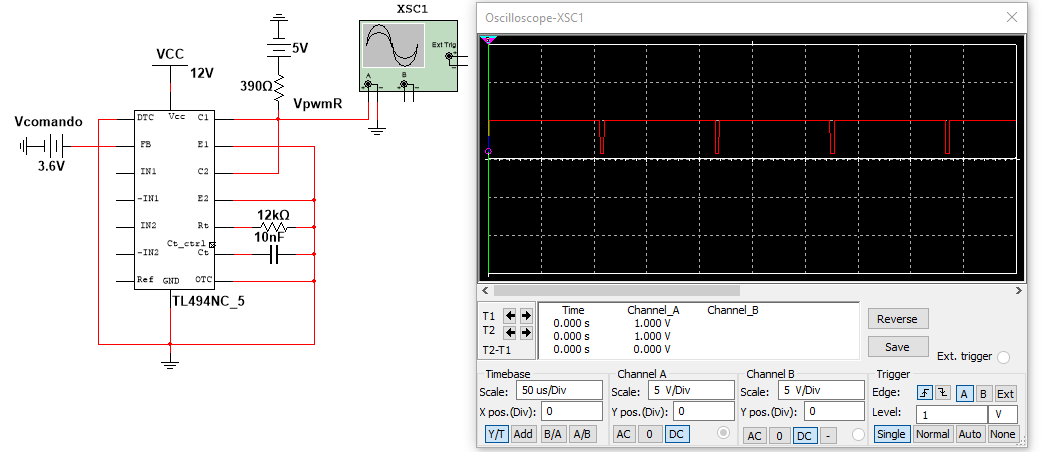
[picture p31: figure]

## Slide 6

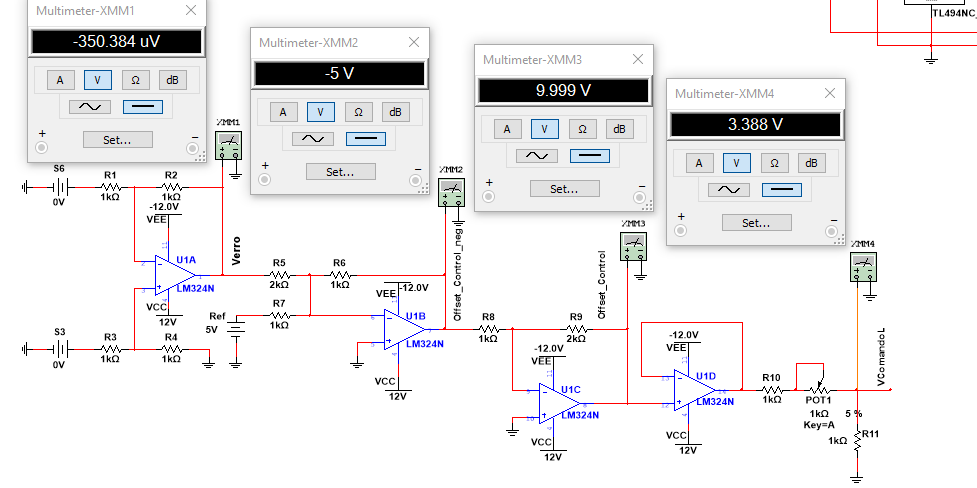
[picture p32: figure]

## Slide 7

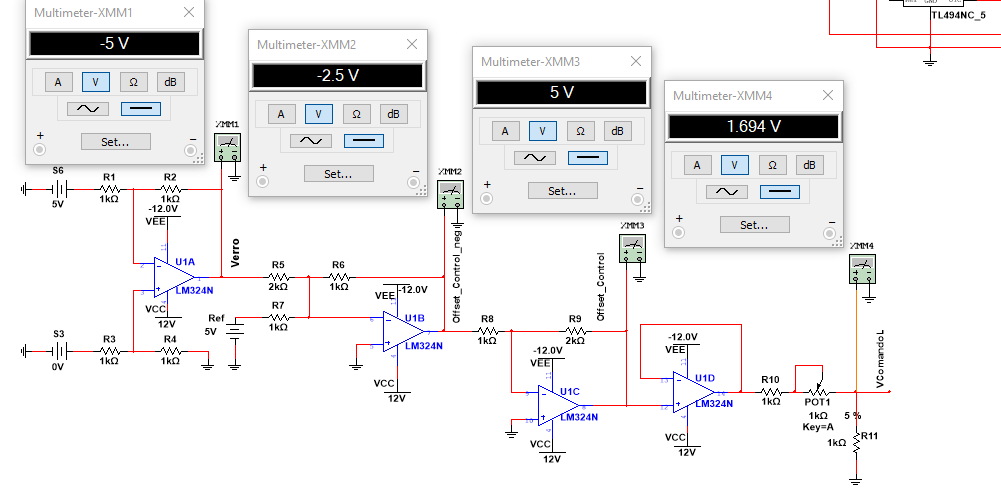
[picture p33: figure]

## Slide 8

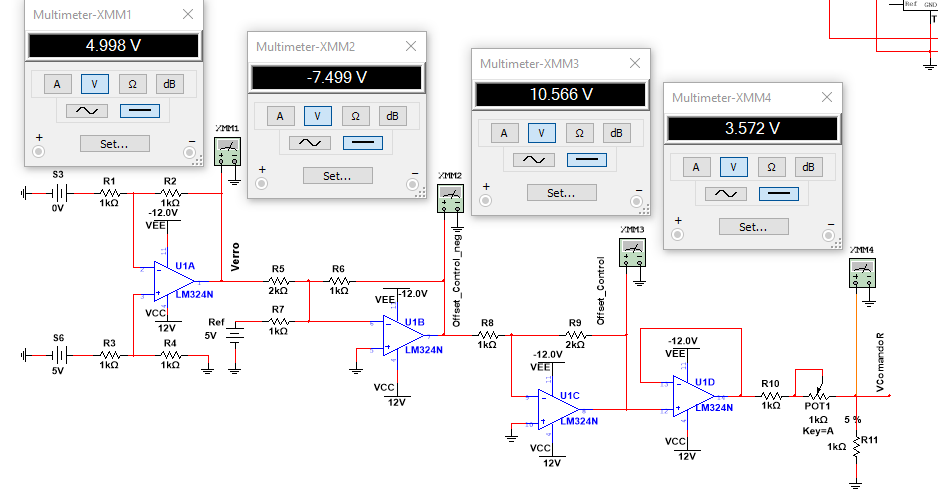
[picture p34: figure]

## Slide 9

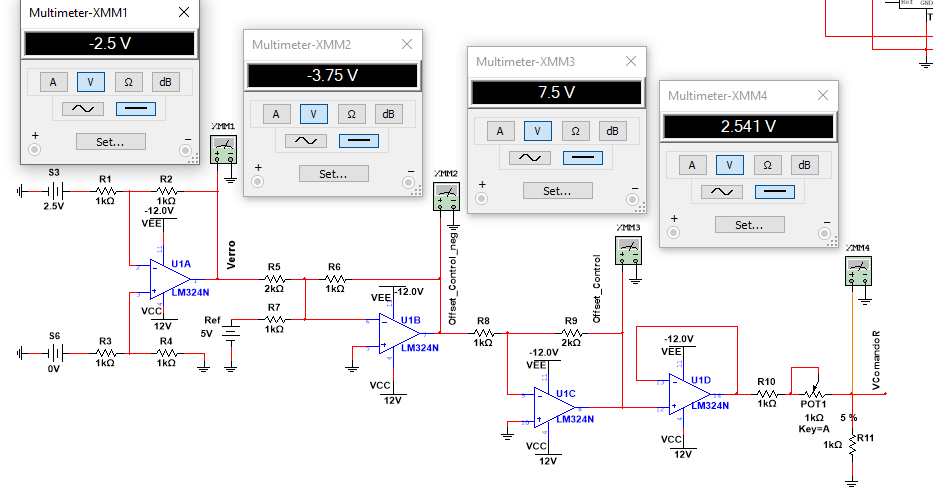
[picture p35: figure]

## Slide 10

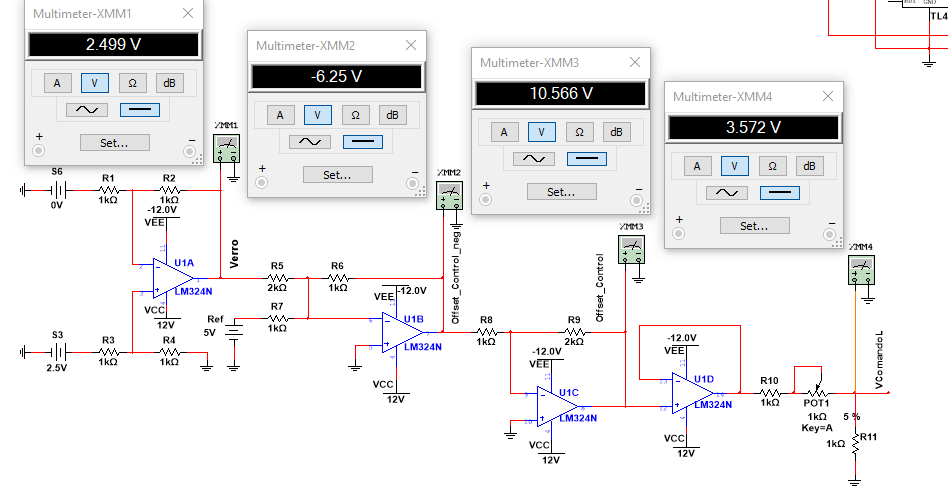
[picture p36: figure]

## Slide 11

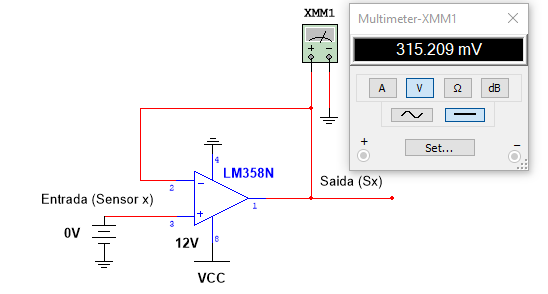
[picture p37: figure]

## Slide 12

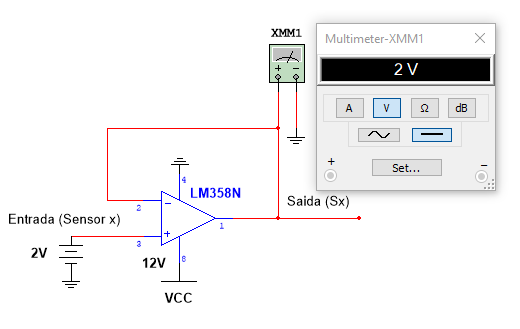
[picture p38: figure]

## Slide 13

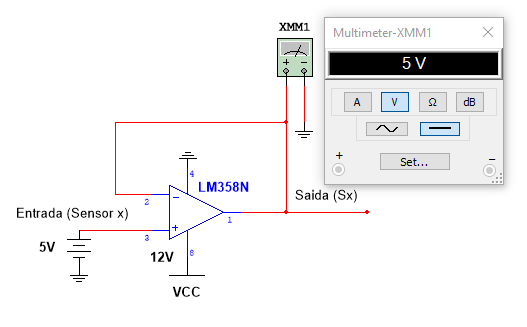
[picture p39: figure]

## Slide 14

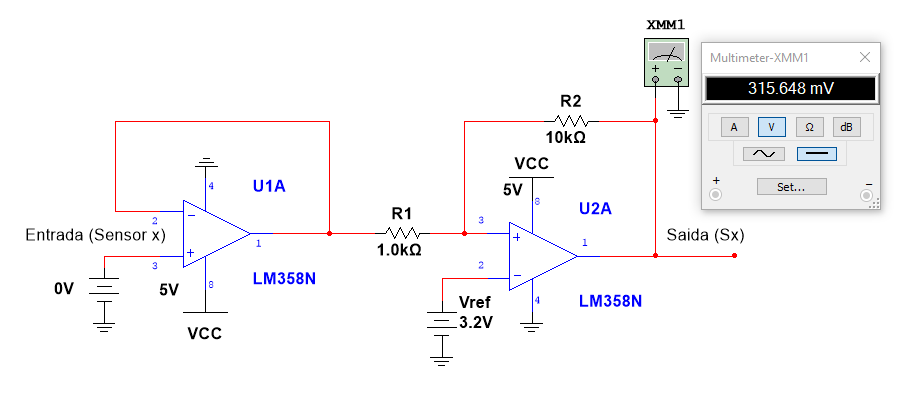
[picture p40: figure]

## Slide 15

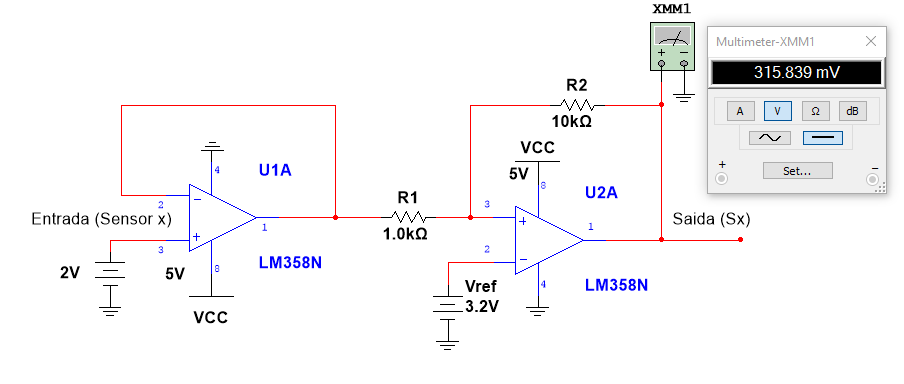
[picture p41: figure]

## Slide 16

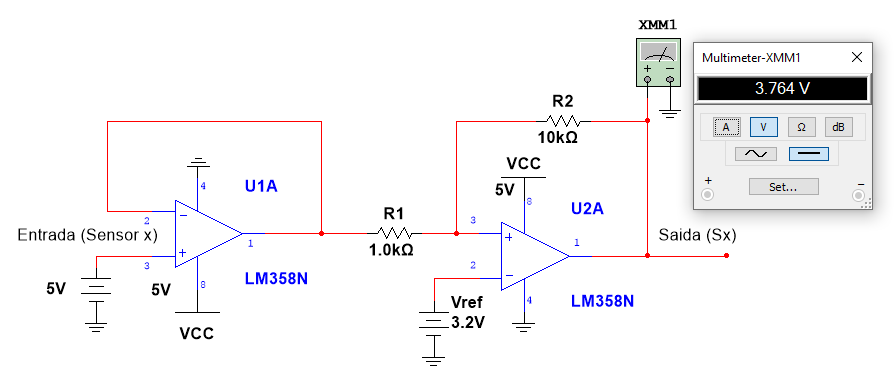
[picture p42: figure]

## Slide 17

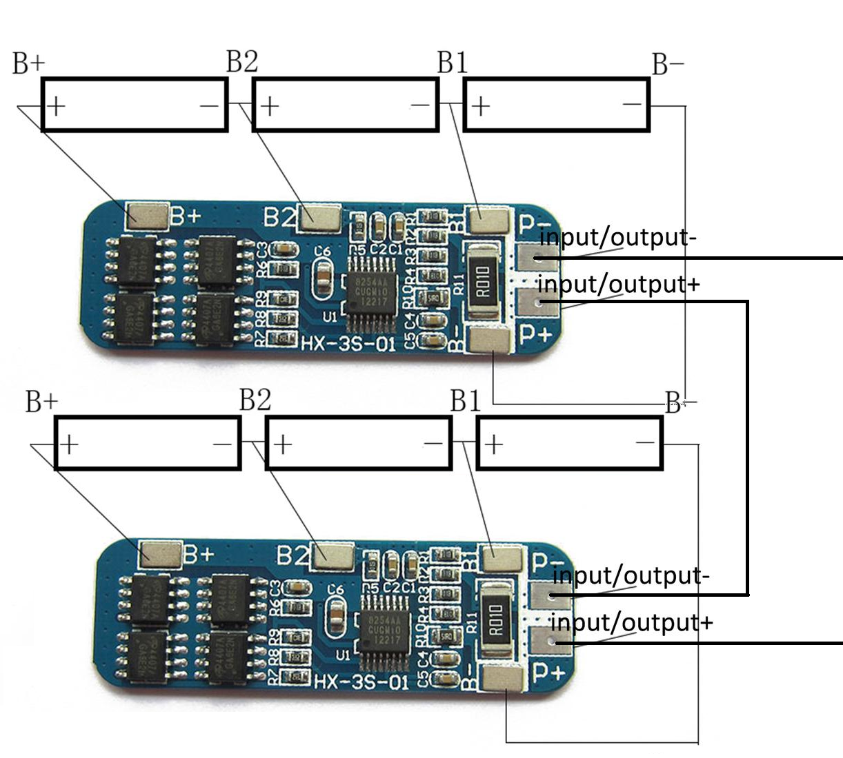
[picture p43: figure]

-12 V

GND

+12 V

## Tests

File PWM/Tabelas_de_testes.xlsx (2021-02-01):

verro | duty
1.15 | 0
1.39 | 10
1.9 | 30
2.3 | 50
2.9 | 70
3.35 | 90
3.6 | 100
vmedida | vref | ganho | verro |  | vmedida | vref | ganho | verro | vmedida | vref | ganho | verro | vmedida | vref | ganho | verro
0.5 | 4 | 1 | 3.5 |  | 0.5 | 5 | 1 | 4.5 | 0.5 | 4 | 4 | 14 | 0.5 | 4 | 1.2 | 4.2
1 | 4 | 1 | 3 |  | 1 | 5 | 1 | 4 | 1 | 4 | 4 | 12 | 1 | 4 | 1.2 | 3.6
1.5 | 4 | 1 | 2.5 |  | 1.5 | 5 | 1 | 3.5 | 1.5 | 4 | 4 | 10 | 1.5 | 4 | 1.2 | 3
2 | 4 | 1 | 2 |  | 2 | 5 | 1 | 3 | 2 | 4 | 4 | 8 | 2 | 4 | 1.2 | 2.4
2.5 | 4 | 1 | 1.5 |  | 2.5 | 5 | 1 | 2.5 | 2.5 | 4 | 4 | 6 | 2.5 | 4 | 1.2 | 1.8
3 | 4 | 1 | 1 |  | 3 | 5 | 1 | 2 | 3 | 4 | 4 | 4 | 3 | 4 | 1.2 | 1.2
3.5 | 4 | 1 | 0.5 |  | 3.5 | 5 | 1 | 1.5 | 3.5 | 4 | 4 | 2 | 3.5 | 4 | 1.2 | 0.6
4 | 4 | 1 | 0 |  | 4 | 5 | 1 | 1 | 4 | 4 | 4 | 0 | 4 | 4 | 1.2 | 0
4.5 | 4 | 1 | -0.5 |  | 4.5 | 5 | 1 | 0.5 | 4.5 | 4 | 4 | -2 | 4.5 | 4 | 1.2 | -0.6
 |  |  |  |  | vmedida | vref | ganho | verro | vmedida | vref | ganho | verro
 |  |  |  |  | 0.5 | 4.9 | 1.6 | 7.04 | 0.5 | 4.5 | 2.2 | 8.8
 |  |  |  |  | 1 | 4.9 | 1.6 | 6.24 | 1 | 4.5 | 2.2 | 7.7
 |  |  |  |  | 1.5 | 4.9 | 1.6 | 5.44 | 1.5 | 4.5 | 2.2 | 6.6
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

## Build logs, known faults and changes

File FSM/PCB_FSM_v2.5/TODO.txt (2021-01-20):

- A porta 74LS14 - Shmitt Trigger é usada na saída do circuito de debounce. Também deverá ser utilizada
para conectar as saídas dos sensores S1 e S8 à PCB da fsm, visto que esses valores poderão não ser exatamente
0 ou 5V, e a Shmitt Trigger compensa isso. Visto que cada 74LS14 tem 4 portas poderemos usar o IC apenas
nesta PCB. Depois só é necessário ligar os S1, S8 e B a um jumper.

- Verificar se quando é retirada a alimentação dos flip flops JK ocorre reset do estado. Ou seja,
verificar se ao ligar o robot após ter sido desligado enquanto estava em andamento, que B1 e B0
iniciam a 0, e não, com os valores dos últimos estados.
 
- Alterei a porta lógica que ligava ás ANDs de saída por uma OR, visto que (B1'&B0')' = B1+B0

- Ter em atenção que algumas entradas dos JK estão negadas. Temos portas NANDs já compradas, caso queiramos usar.
Além disso temos OR, AND, NOT, Shmitt Trigger, NAND, JK e NE555.

- Ter em atenção que vamos ter 4 jumpers de saída, para ligar ao Driver.

- Ver se vale a pena pôr LEDs para indicar o estado atual, em B0 e B1.

------------------- 02/01/2021 ------------------

- NE555: confirmar o IC; verificar se as portas deste IC são negadas (no PADS estão RES, THR e DIS).

- Dilema: Usar varios IC e menos ligações vs minimo de ICs e ligações mais complicadas.

- Verificar se foram usados os componentes corretos, tais como condensadores e resistencias.

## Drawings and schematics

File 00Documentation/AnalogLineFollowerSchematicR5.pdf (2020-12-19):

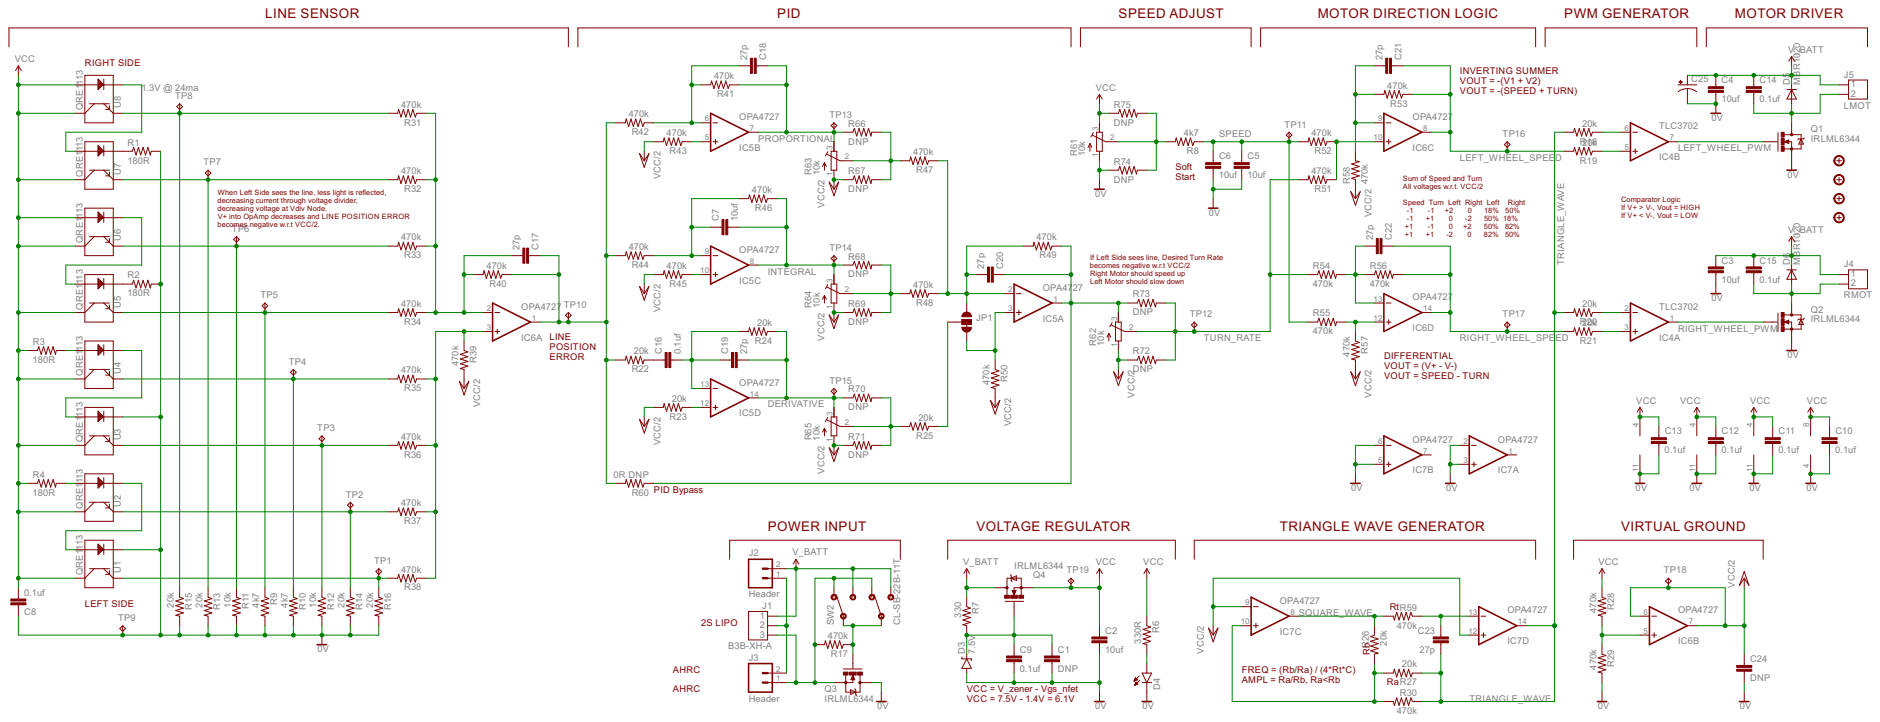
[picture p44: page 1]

INVERTING SUMMER
VOUT = -(V1 + V2) VOUT = -(SPEED + TURN)

When Left Side sees the line, less light is reflected, decreasing current through voltage divider, decreasing voltage at Vdiv Node. V+ into OpAmp decreases and LINE POSITION ERROR

If Left Side sees line, Desired Turn Rate
becomes negative w.r.t VCC/2 Right Motor should speed up

Left Motor should slow down

DIFFERENTIAL VOUT = (V+ - V-) VOUT = SPEED - TURN

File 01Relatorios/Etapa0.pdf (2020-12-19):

# AWR – 19

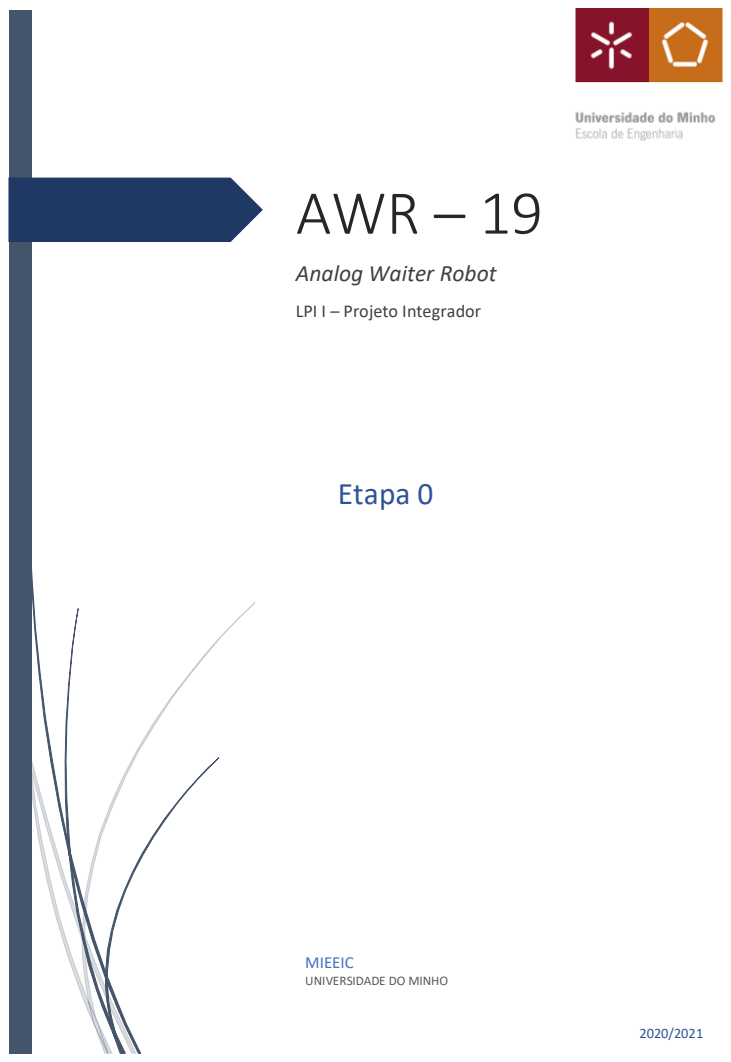
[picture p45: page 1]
Etapa 0

Analog Waiter Robot

LPI I – Projeto Integrador

MIEEIC
UNIVERSIDADE DO MINHO

1

### Grupo:

- Bruno Miguel Vasconcelos da Silva 88289
- Diogo Miguel Cunha Fernandes 88262
- Duarte Miguel Novo Rodrigues 88259
- Francisco Lopes Salgado 88231
- João Pedro Dias Miranda 88237
- José Tomás Lima de Abreu, 88218

### Coordenador / líder:

- João Pedro Dias Miranda 88237

### Orientador:

- Luís André Magalhães de Barros

### Nome do projeto:

- Analog Waiter Robot – 19 (AWR -19)

### Ideia do Produto:

A ideia do produto surgiu da necessidade de atuar perante o panorama pandémico (Covid-19), mais propriamente no auxílio a pessoas que se encontrem em isolamento.

Como todos sabemos, uma pessoa em isolamento não pode ter contacto com o mundo exterior. Por este motivo, pensámos em desenvolver um robô que faça chegar os bens essenciais à pessoa em isolamento.

A função principal do produto será desempenhar o papel de um “empregado de mesa”, daí o nome “Waiter”. O termo “Analog” advém do facto de todas funcionalidades serem implementadas de forma analógica, perfazendo o nome do robô “Analog Waiter Robot”.

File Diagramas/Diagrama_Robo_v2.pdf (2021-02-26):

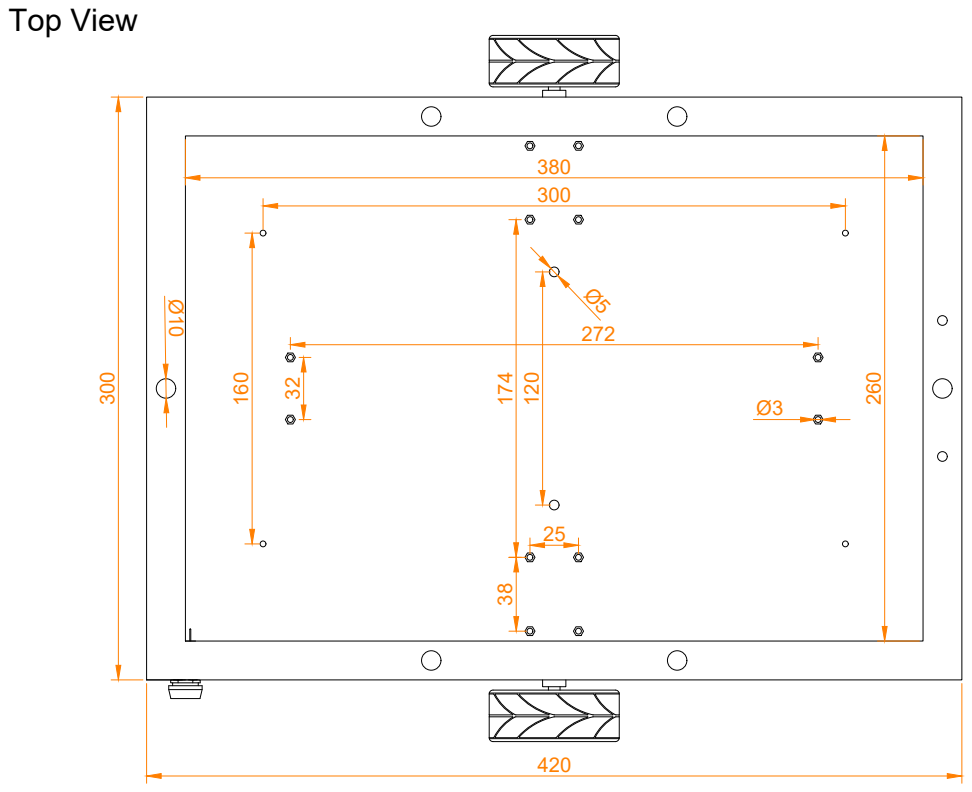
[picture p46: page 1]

260 Top View Bottom View

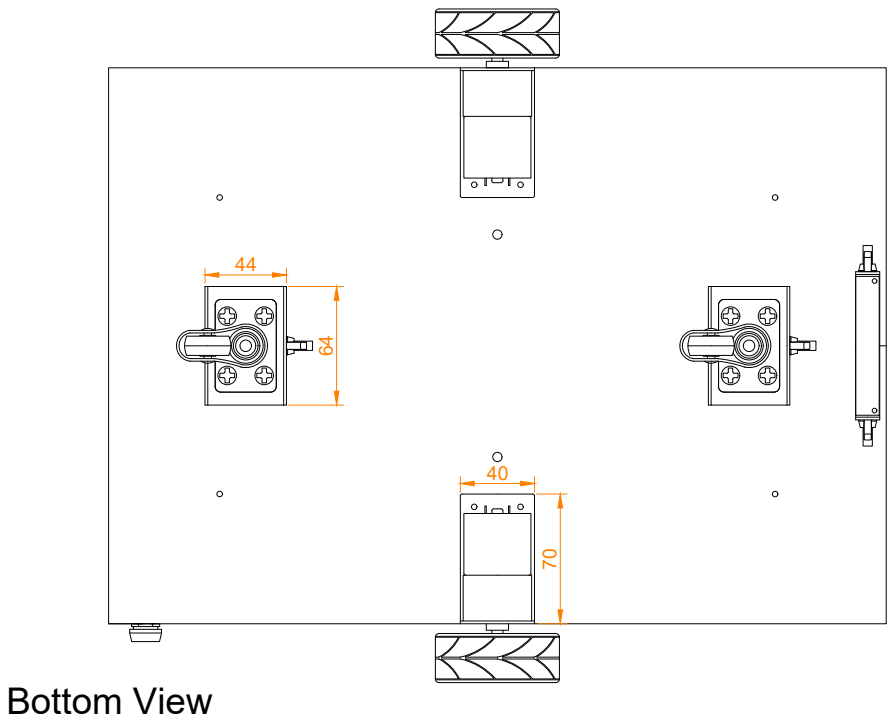
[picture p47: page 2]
Bottom View

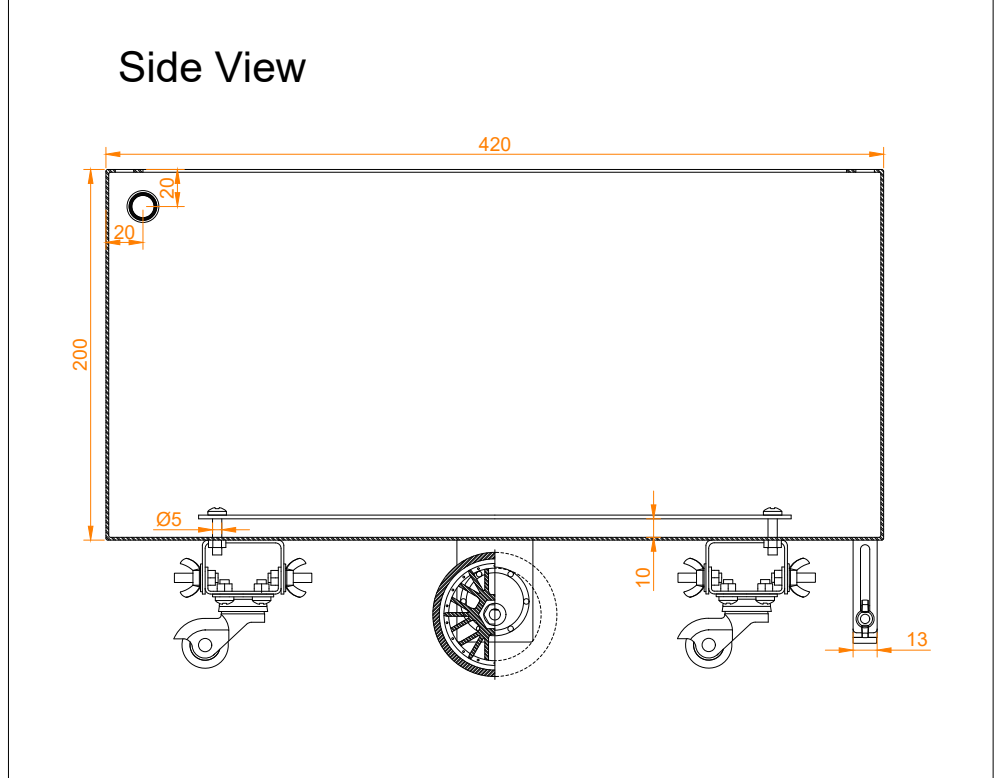
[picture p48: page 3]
Side View

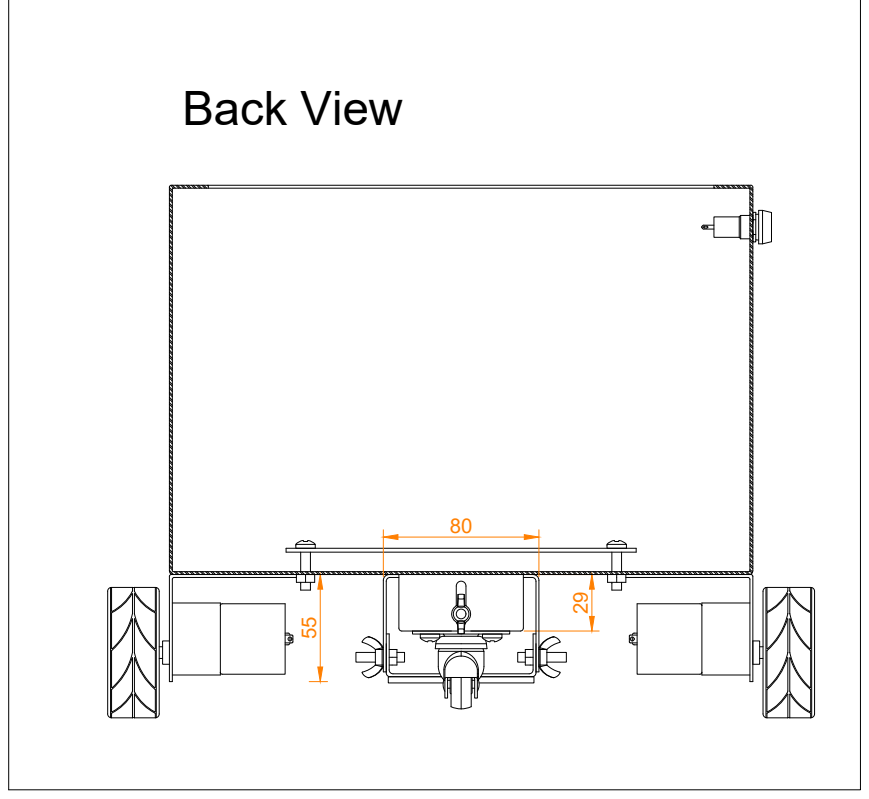
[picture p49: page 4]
Back View

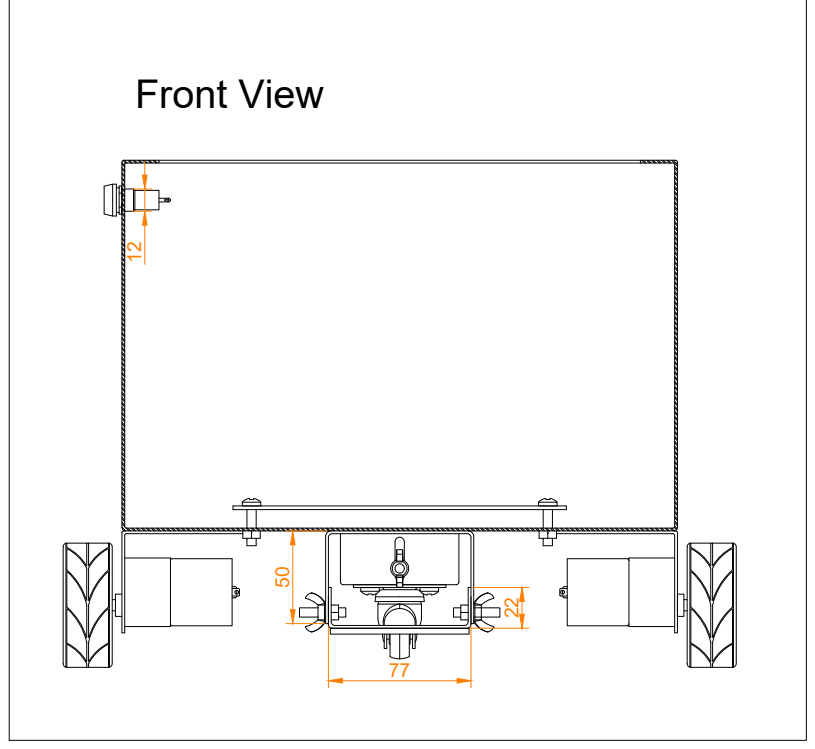
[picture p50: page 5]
Front View

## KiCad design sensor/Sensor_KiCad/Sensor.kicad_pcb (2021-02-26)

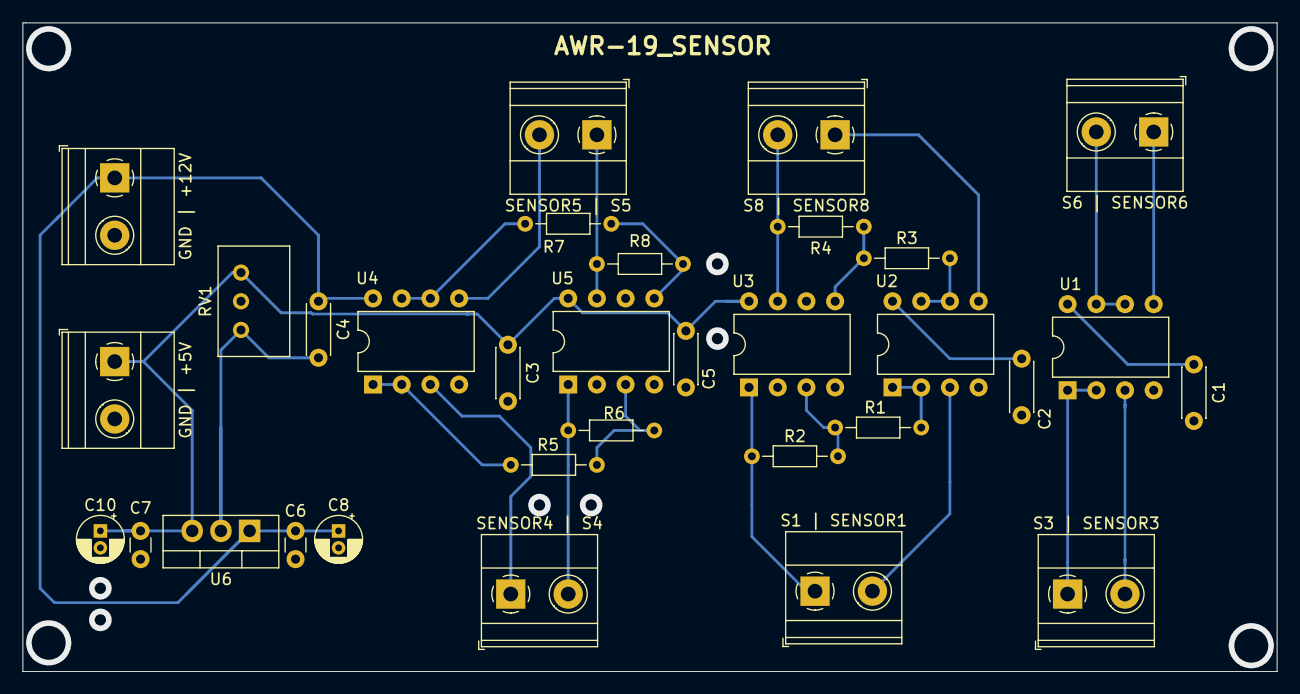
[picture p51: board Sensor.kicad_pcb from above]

Board: 2 copper layers, 111.0 x 57.4 mm, 32 parts (0 on the bottom side), 24 nets.

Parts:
C1, C2, C3, C4, C5: C; C_Disc_D4.3mm_W1.9mm_P5.00mm
C6, C7: C; C_Disc_D3.0mm_W1.6mm_P2.50mm
C8, C10: CP_Small; CP_Radial_D4.0mm_P1.50mm
GND | +5V, GND | +12V: Conn_01x02_Female; TerminalBlock_Phoenix_MKDS-1,5-2-5.08_1x02_P5.08mm_Horizont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
R1, R3: 1k; R_Axial_DIN0204_L3.6mm_D1.6mm_P7.62mm_Horizontal
R2, R4: 10k; R_Axial_DIN0204_L3.6mm_D1.6mm_P7.62mm_Horizontal
R5, R6, R7, R8: R; R_Axial_DIN0204_L3.6mm_D1.6mm_P7.62mm_Horizontal
RV1: R_POT; Potentiometer_Bourns_3299W_Vertical
S1 | SENSOR1, S3 | SENSOR3, S6 | SENSOR6, S8 | SENSOR8: Conn_01x02_Female; TerminalBlock_Phoenix_MKDS-1,5-2-5.08_1x02_P5.08mm_Horizont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
SENSOR4 | S4, SENSOR5 | S5: Conn_01x02_Female; TerminalBlock_Phoenix_MKDS-1,5-2-5.08_1x02_P5.08mm_Horizont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
U1, U2, U3, U4, U5: LM358; DIP-8_W7.62mm
U6: LM7805_TO220; TO-220-3_Vertical

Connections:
+5V: C3.1, C5.1, C7.1, C10.1, GND | +5V.1, RV1.1, U3.8, U5.8, U6.3
+12V: C1.1, C2.1, C4.1, C6.1, C8.1, GND | +12V.1, U1.8, U2.8, U4.8, U6.1
GND: C1.2, C2.2, C3.2, C4.2, C5.2, C6.2, C7.2, C8.2, C10.2, GND | +5V.2, GND | +12V.2, RV1.3, U1.4, U2.4, U3.4, U4.4, U5.4, U6.2
IN_SENSOR1: S1 | SENSOR1.2, U2.3
IN_SENSOR3: S3 | SENSOR3.2, U1.3
IN_SENSOR4: SENSOR4 | S4.1, U4.3
IN_SENSOR5: SENSOR5 | S5.2, U4.5
IN_SENSOR6: S6 | SENSOR6.1, U1.5
IN_SENSOR8: S8 | SENSOR8.1, U2.5
unnamed: R1.1, U2.1, U2.2
unnamed: R1.2, R2.1, U3.3
unnamed: R3.1, U2.6, U2.7
unnamed: R3.2, R4.1, U3.5
unnamed: R5.1, U4.1, U4.2
unnamed: R5.2, R6.1, U5.3
unnamed: R7.1, U4.6, U4.7
unnamed: R7.2, R8.1, U5.5
OUT_SENSOR1: R2.2, S1 | SENSOR1.1, U3.1
OUT_SENSOR3: S3 | SENSOR3.1, U1.1, U1.2
OUT_SENSOR4: R6.2, SENSOR4 | S4.2, U5.1
OUT_SENSOR5: R8.2, SENSOR5 | S5.1, U5.7
OUT_SENSOR6: S6 | SENSOR6.2, U1.6, U1.7
OUT_SENSOR8: R4.2, S8 | SENSOR8.2, U3.7
VREF: RV1.2, U3.2, U3.6, U5.2, U5.6

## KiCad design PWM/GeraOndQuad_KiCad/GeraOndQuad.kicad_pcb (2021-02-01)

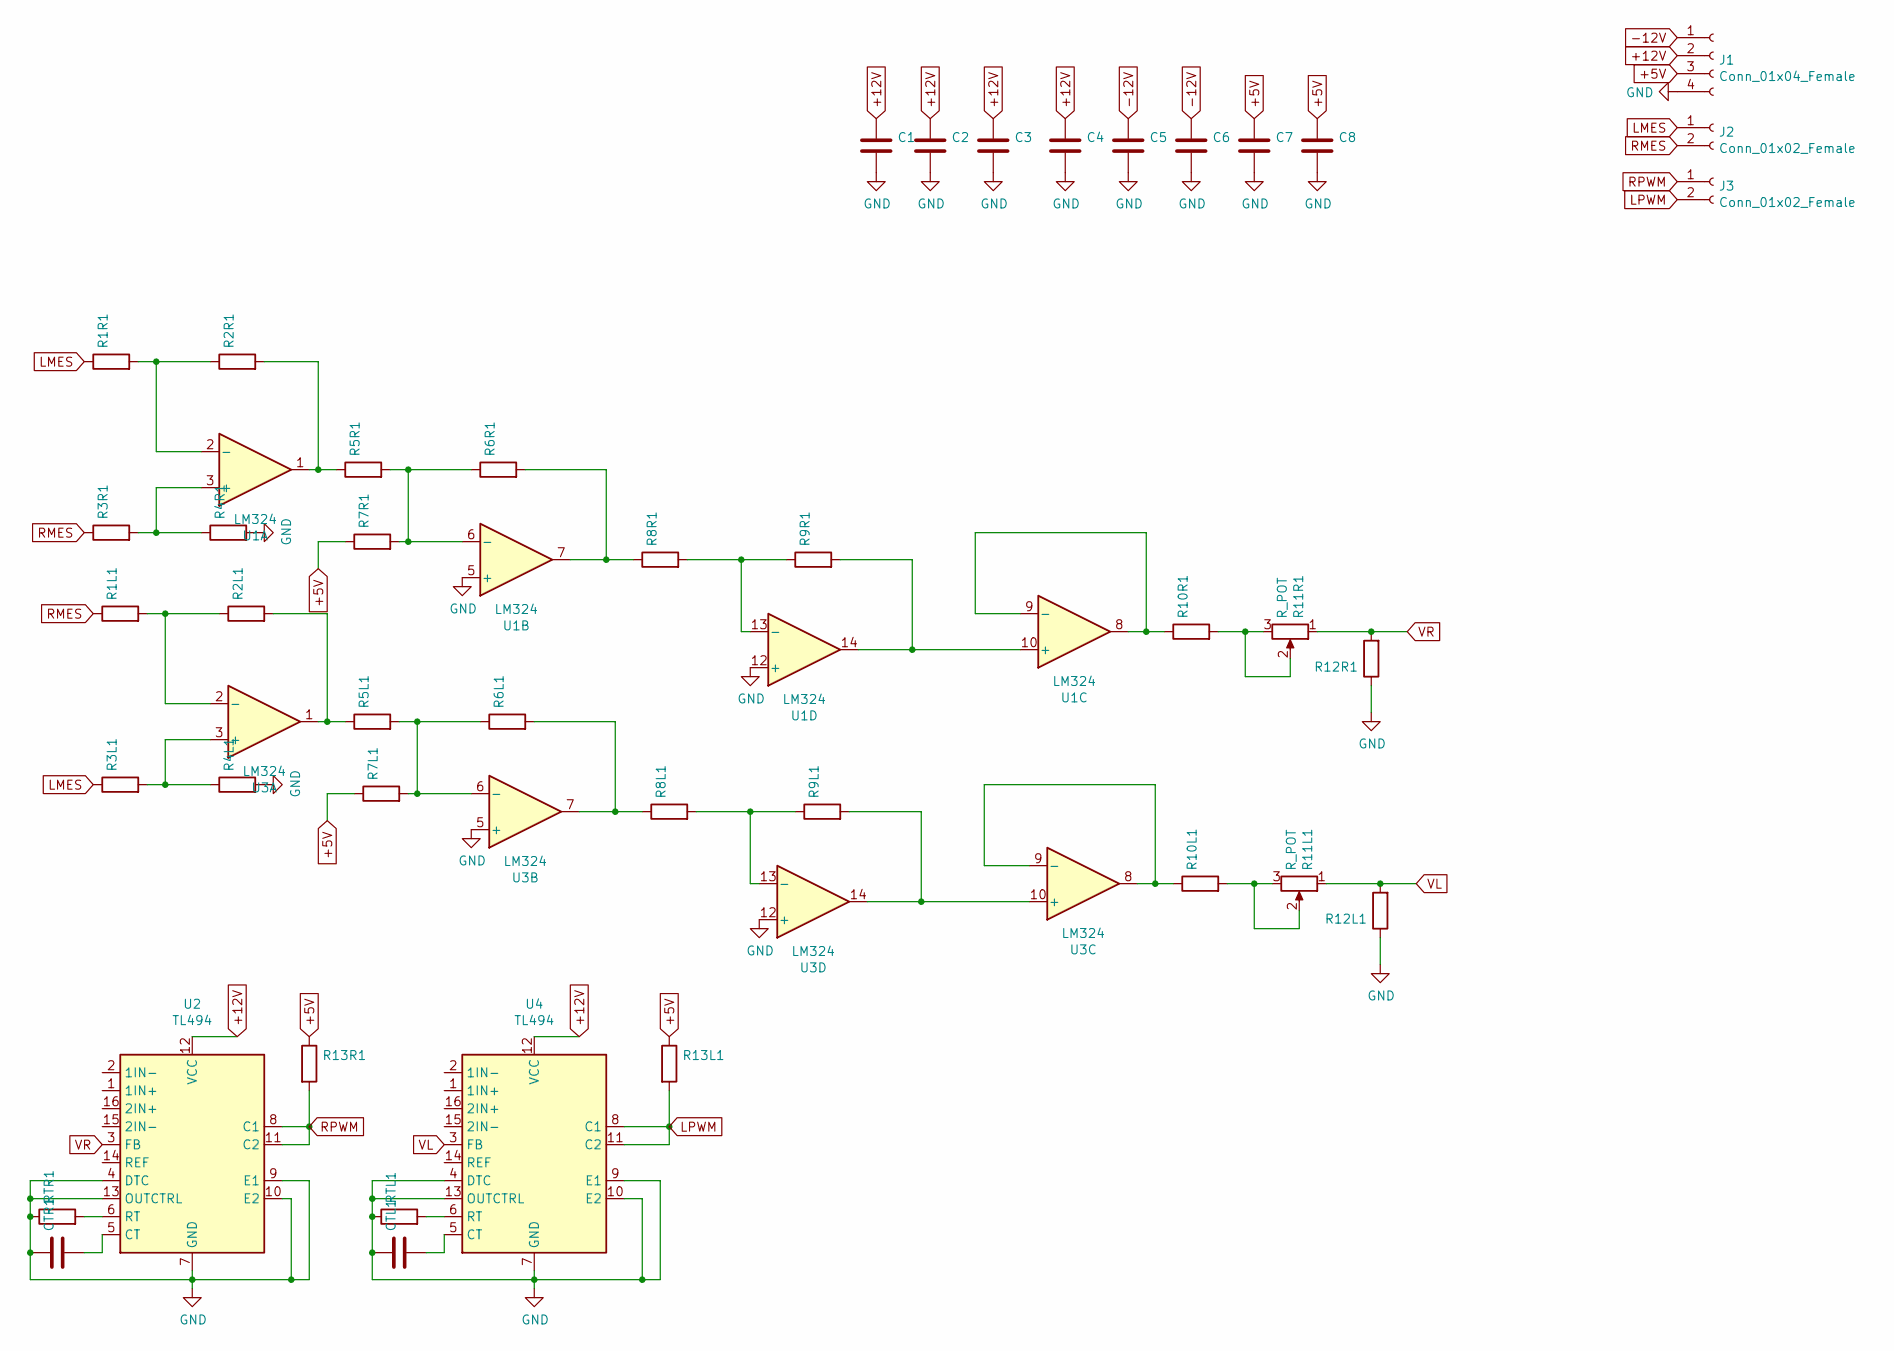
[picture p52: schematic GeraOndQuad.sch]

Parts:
C1, C2, C3, C4, C5, C6, C7, C8: C; C_Disc_D3.0mm_W1.6mm_P2.50mm
CTL1: C; C_Disc_D3.0mm_W1.6mm_P2.50mm
CTR1: C; C_Disc_D3.0mm_W1.6mm_P2.50mm
J1: Conn_01x04_Female; TerminalBlock_Phoenix_MKDS-1,5-4_1x04_P5.00mm_Horizontal
J2, J3: Conn_01x02_Female; TerminalBlock_Phoenix_MKDS-1,5-2-5.08_1x02_P5.08mm_Horizont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
R1L1, R1R1, R2L1, R2R1, R3L1, R3R1, R4L1, R4R1, R5L1, R5R1, R6L1, R6R1, R7L1, R7R1, R8L1, R8R1, R9L1, R9R1, R10L1, R10R1, R12L1, R12R1, R13L1, R13R1: R; R_Axial_DIN0204_L3.6mm_D1.6mm_P7.62mm_Horizontal
R11L1, R11R1: R_POT; Potentiometer_Bourns_3299W_Vertical
RTL1: R; R_Axial_DIN0204_L3.6mm_D1.6mm_P7.62mm_Horizontal
RTR1: R; R_Axial_DIN0204_L3.6mm_D1.6mm_P7.62mm_Horizontal
U1, U3: LM324; DIP-14_W7.62mm
U2, U4: TL494; DIP-16_W10.16mm

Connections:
+5V: C7.1, C8.1, J1.3, R7L1.1, R7R1.1, R13L1.1, R13R1.1; also elsewhere on the board
+12V: C1.1, C2.1, C3.1, C4.1, J1.2, U1.4 (V+), U2.12 (VCC), U3.4 (V+), U4.12 (VCC); also elsewhere on the board
-12V: C5.1, C6.1, J1.1, U1.11 (V-), U3.11 (V-); also elsewhere on the board
GND: C1.2, C2.2, C3.2, C4.2, C5.2, C6.2, C7.2, C8.2, CTL1.1, CTR1.1, J1.4, R4L1.2, R4R1.2, R12L1.1, R12R1.1, RTL1.1, RTR1.1, U1.5 (+), U1.12 (+), U2.4 (DTC), U2.7 (GND), U2.9 (E1), U2.10 (E2), U2.13 (OUTCTRL), U3.5 (+), U3.12 (+), U4.4 (DTC), U4.7 (GND), U4.9 (E1), U4.10 (E2), U4.13 (OUTCTRL); also elsewhere on the board
LMES: J2.1, R1R1.1, R3L1.1; also elsewhere on the board
LPWM: J3.2, R13L1.2, U4.8 (C1), U4.11 (C2); also elsewhere on the board
unnamed: CTL1.2, U4.5 (CT)
unnamed: CTR1.2, U2.5 (CT)
unnamed: R1L1.2, R2L1.1, U3.2 (-)
unnamed: R1R1.2, R2R1.1, U1.2 (-)
unnamed: R2L1.2, R5L1.1, U3.1
unnamed: R2R1.2, R5R1.1, U1.1
unnamed: R3L1.2, R4L1.1, U3.3 (+)
unnamed: R3R1.2, R4R1.1, U1.3 (+)
unnamed: R5L1.2, R6L1.1, R7L1.2, U3.6 (-)
unnamed: R5R1.2, R6R1.1, R7R1.2, U1.6 (-)
unnamed: R6L1.2, R8L1.1, U3.7
unnamed: R6R1.2, R8R1.1, U1.7
unnamed: R8L1.2, R9L1.1, U3.13 (-)
unnamed: R8R1.2, R9R1.1, U1.13 (-)
unnamed: R9L1.2, U3.10 (+), U3.14
unnamed: R9R1.2, U1.10 (+), U1.14
unnamed: R10L1.1, U3.8, U3.9 (-)
unnamed: R10L1.2, R11L1.2, R11L1.3
unnamed: R10R1.1, U1.8, U1.9 (-)
unnamed: R10R1.2, R11R1.2, R11R1.3
unnamed: RTL1.2, U4.6 (RT)
unnamed: RTR1.2, U2.6 (RT)
RMES: J2.2, R1L1.1, R3R1.1; also elsewhere on the board
RPWM: J3.1, R13R1.2, U2.8 (C1), U2.11 (C2); also elsewhere on the board
VL: R11L1.1, R12L1.2, U4.3 (FB)
VR: R11R1.1, R12R1.2, U2.3 (FB)

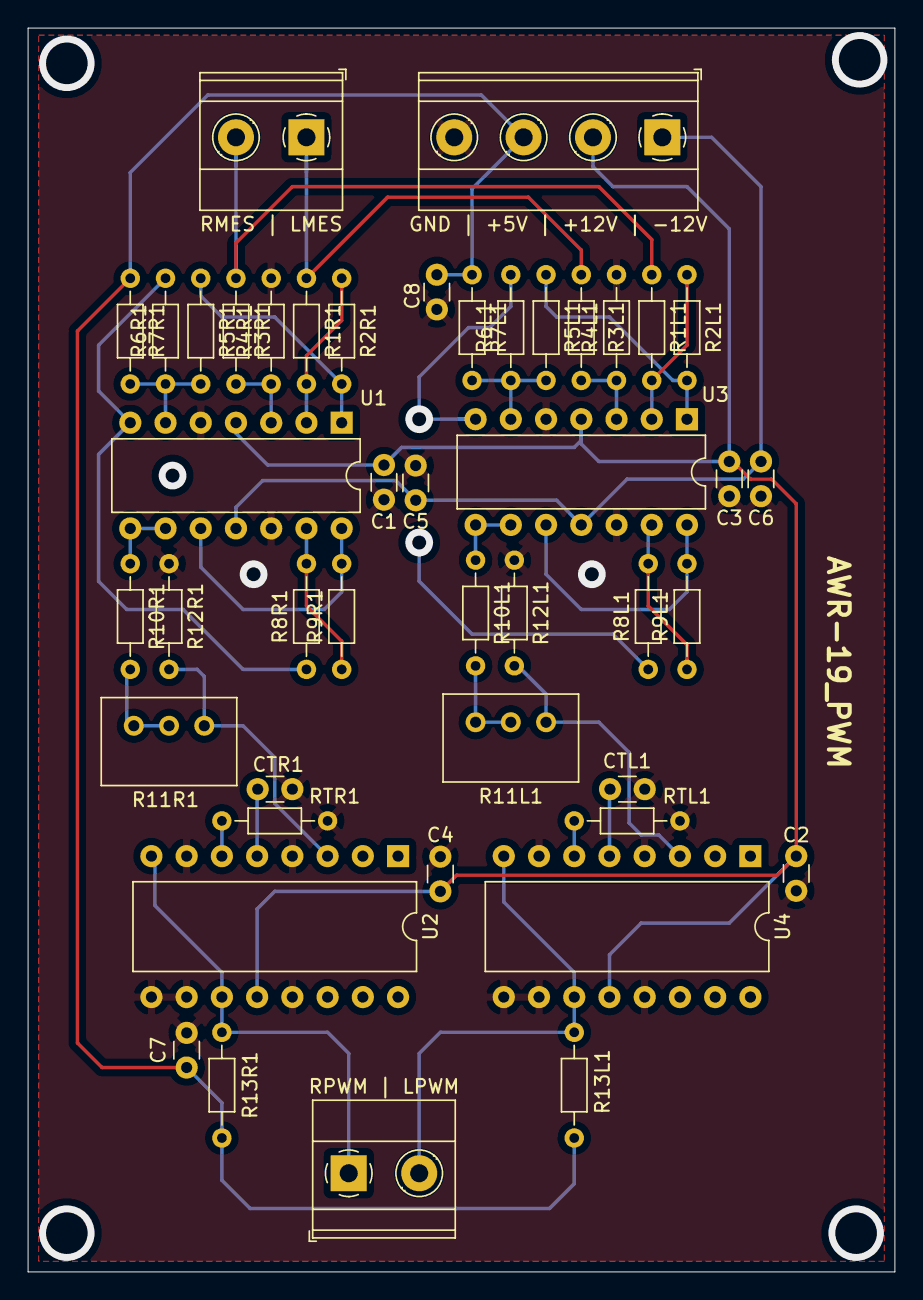
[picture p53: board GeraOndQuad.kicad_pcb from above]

Board: 2 copper layers, 62.5 x 89.7 mm, 45 parts (0 on the bottom side), 32 nets.

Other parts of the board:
GND | +5V | +12V | -12V: Conn_01x04_Female; TerminalBlock_Phoenix_MKDS-1,5-4_1x04_P5.00mm_Horizontal
RMES | LMES: Conn_01x02_Female; TerminalBlock_Phoenix_MKDS-1,5-2-5.08_1x02_P5.08mm_Horizont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
RPWM | LPWM: Conn_01x02_Female; TerminalBlock_Phoenix_MKDS-1,5-2-5.08_1x02_P5.08mm_Horizont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

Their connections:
+5V: GND | +5V | +12V | -12V.3; also elsewhere on the board
+12V: GND | +5V | +12V | -12V.2; also elsewhere on the board
-12V: GND | +5V | +12V | -12V.1; also elsewhere on the board
GND: GND | +5V | +12V | -12V.4; also elsewhere on the board
LMES: RMES | LMES.1; also elsewhere on the board
LPWM: RPWM | LPWM.2; also elsewhere on the board
RMES: RMES | LMES.2; also elsewhere on the board
RPWM: RPWM | LPWM.1; also elsewhere on the board

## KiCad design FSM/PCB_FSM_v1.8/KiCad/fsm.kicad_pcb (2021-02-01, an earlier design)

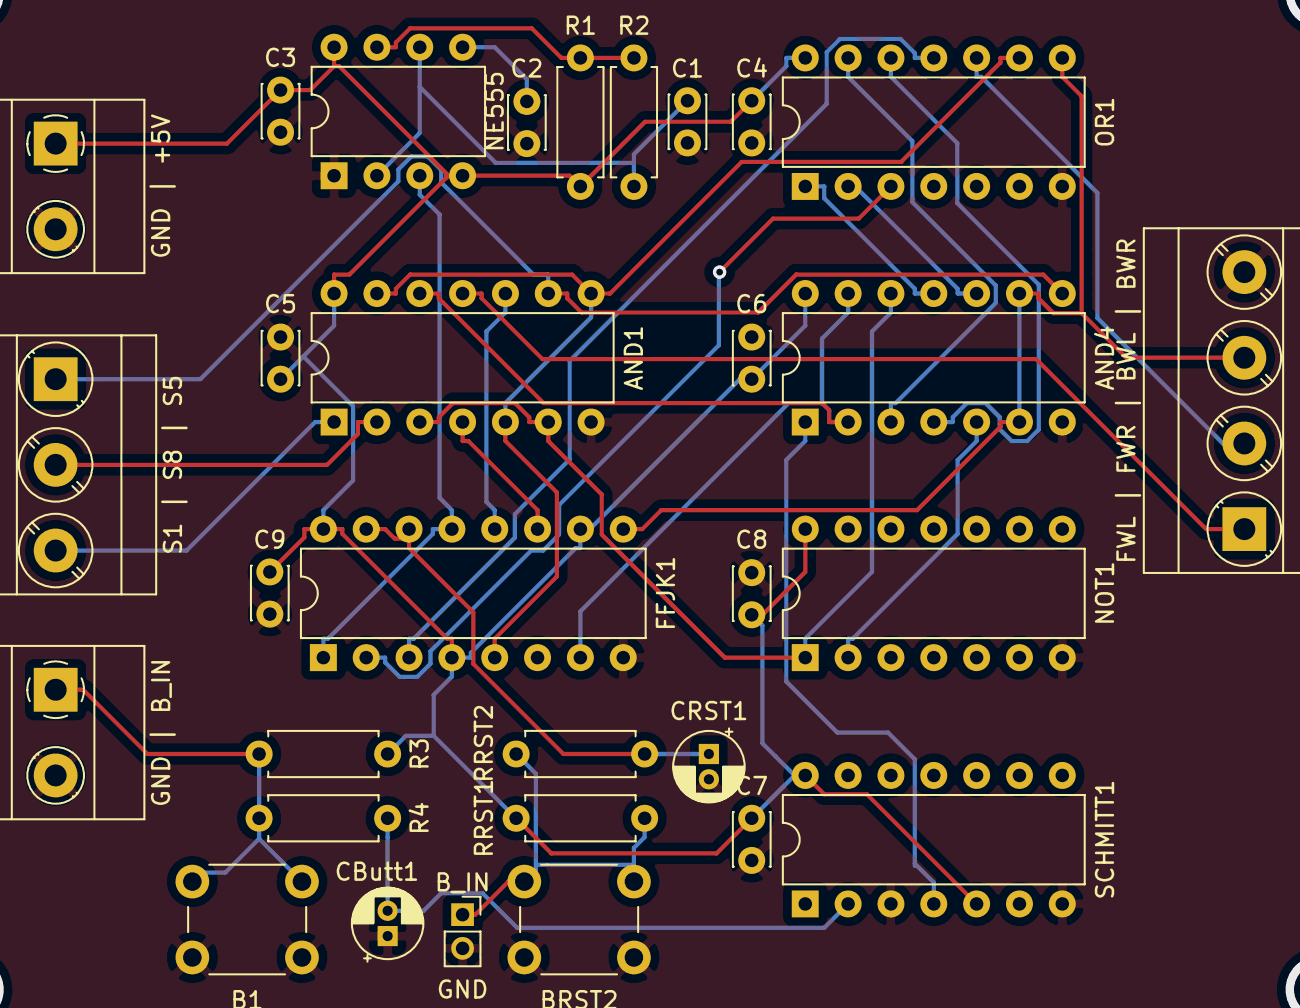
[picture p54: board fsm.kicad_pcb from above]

Board: 2 copper layers, 31 parts (0 on the bottom side), 29 nets.

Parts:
AND1, AND4: 4081; DIP-14_W7.62mm
B1: SW_Push; SW_PUSH_6mm_H7.3mm
BRST2: SW_Push; SW_PUSH_6mm_H7.3mm
C1: 4,7u; C_Disc_D3.0mm_W2.0mm_P2.50mm
C2, C3, C4, C5, C6, C7, C8, C9: 10n; C_Disc_D3.0mm_W2.0mm_P2.50mm
CButt1: 10n; CP_Radial_D4.0mm_P1.50mm
CRST1: 10n; CP_Radial_D4.0mm_P1.50mm
FFJK1: 74LS76; DIP-16_W7.62mm
FWL | FWR | BWL | BWR: Conn_01x04_Female; TerminalBlock_Phoenix_MKDS-3-4-5.08_1x04_P5.08mm_Horizontal
GND: Conn_01x02_Female; PinSocket_1x02_P2.00mm_Vertical
GND | +5V: Conn_01x02_Female; TerminalBlock_Phoenix_MKDS-1,5-2-5.08_1x02_P5.08mm_Horizont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
GND | B_IN: Conn_01x02_Female; TerminalBlock_Phoenix_MKDS-1,5-2-5.08_1x02_P5.08mm_Horizont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
NE555: NE555P; DIP-8_W7.62mm
NOT1: 74LS04; DIP-14_W7.62mm
OR1: 4071; DIP-14_W7.62mm
R1: 6,2k; R_Axial_DIN0207_L6.3mm_D2.5mm_P7.62mm_Horizontal
R2: 150k; R_Axial_DIN0207_L6.3mm_D2.5mm_P7.62mm_Horizontal
R3: 10k; R_Axial_DIN0207_L6.3mm_D2.5mm_P7.62mm_Horizontal
R4: 1k; R_Axial_DIN0207_L6.3mm_D2.5mm_P7.62mm_Horizontal
RRST1, RRST2: 100k; R_Axial_DIN0207_L6.3mm_D2.5mm_P7.62mm_Horizontal
S1 | S8 | S5: Conn_01x03_Female; TerminalBlock_Phoenix_MKDS-3-3-5.08_1x03_P5.08mm_Horizontal
SCHMITT1: SN74LVC1G14DRL; DIP-14_W7.62mm

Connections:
+5V: AND1.14, AND4.14, C3.1, C4.1, C5.1, C6.1, C7.1, C8.1, C9.1, FFJK1.4, FFJK1.10, FFJK1.16, GND | +5V.1, NE555.4, NE555.8, NOT1.14, OR1.14, R1.1, R3.1, RRST1.1, SCHMITT1.5, SCHMITT1.14
B: AND4.1, SCHMITT1.4
B0: AND1.5, AND1.8, AND1.13, FFJK1.5, OR1.9
B1': AND1.12, AND4.2, AND4.13, FFJK1.7
BWL: AND4.6, AND4.9, FFJK1.9, FWL | FWR | BWL | BWR.3, OR1.8
B_IN: B1.2, GND | B_IN.1, R3.2, R4.1
CLK: FFJK1.1, FFJK1.13, NE555.3
FWL: AND1.11, FWL | FWR | BWL | BWR.1
FWR: FWL | FWR | BWL | BWR.2, OR1.10
GND: AND1.7, AND4.7, B1.1, BRST2.1, C1.2, C2.1, C3.2, C4.2, C5.2, C6.2, C7.2, C8.2, C9.2, CButt1.1, CRST1.2, FFJK1.8, FWL | FWR | BWL | BWR.4, GND.2, GND | +5V.2, GND | B_IN.2, NE555.1, NOT1.7, OR1.7, SCHMITT1.3, SCHMITT1.7
unnamed: AND1.3, AND1.6, AND4.12, NOT1.1
unnamed: AND1.4, FFJK1.11
unnamed: AND1.10, FFJK1.12
unnamed: AND4.3, OR1.13
unnamed: AND4.4, OR1.12
unnamed: AND4.5, NOT1.2
unnamed: AND4.10, OR1.2
unnamed: AND4.11, OR1.1
unnamed: BRST2.2, GND.1, RRST1.2, RRST2.1
unnamed: C1.1, NE555.2, NE555.6, R2.2
unnamed: C2.2, NE555.5
unnamed: CButt1.2, R4.2, SCHMITT1.2
unnamed: FFJK1.2, OR1.3
unnamed: FFJK1.3, OR1.11
unnamed: NE555.7, R1.2, R2.1
RESET: CRST1.1, FFJK1.14, FFJK1.15, RRST2.2
S1: AND1.1, S1 | S8 | S5.3
S5: AND1.9, AND4.8, S1 | S8 | S5.1
S8: AND1.2, S1 | S8 | S5.2

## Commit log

2020-12-19 Added old updates.
    [FSM_v1.1.xlsx, FSM_v1.4.xlsx, FSM_v1.7.xlsx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]
2020-12-23 2.3 correction and 2.4
    [FSM_v2.3.xlsx, FSM_v2.4.xlsx]
2020-12-24 add components and prices
    [Material(Preco).xlsx]
2020-12-29 Added templates for PADs projects.
    [debounce.sch, fsm.sch]
2020-12-29 Added some notes - TODO.txt!
    [fsm.sch]
2020-12-30 Added push button pinout to /resources
2021-01-02 Adding some connections, in and out jumpers. Please, checkout TODO.txt.
    [fsm.sch]
2021-01-07 FSM/PCB_FSM/fsm_design_reduced is not working. Multisim bug i think
2021-01-20 Version 2.5 currently working
    [fsm.sch]
2021-01-20 Starting pcb_fsm
    [fsm.sch]
2021-01-21 Working on pcb_fsm
    [fsm.sch]
2021-01-23 PWM generator without a reference
    [gerOndaQua.sch]
2021-01-23 correction of some error
    [gerOndaQua.sch]
2021-01-23 sensor circuits
    [Sensor.sch]
2021-01-24 added excel with tests
    [Tabelas_de_testes.xlsx]
2021-01-24 last version pads layout (with errors)
    [gerOndaQua.sch]
2021-01-24 maybe it needs +12V on top
    [Sensor.sch]
2021-01-25 Working on fsm_pcb
    [fsm.sch]
2021-01-25 PCB almost finished - no errors
    [Sensor.sch]
2021-01-25 Added fsm_v1.8
    [FSM_v1.8.xlsx]
2021-01-25 PCB v1.8
    [fsm.sch]
2021-01-25 PCB first changes
    [fsm.sch]
2021-01-25 sensor and pwm pcb finished
    [gerOndaQua.sch]
2021-01-25 holy shit
    [fsm.sch]
2021-01-25 added voltagegenerator
    [voltageregulator.sch]
2021-01-26 Sensor PCB finished
    [Sensor.sch]
2021-01-26 decoupling capacitors
    [gerOndaQua.sch]
2021-01-26 added voltage generator PCB
    [voltageregulator.sch]
2021-01-26 FSM Relatorio Final
    [FSM_v1.8.xlsx]
2021-01-26 minor errors corrected
    [gerOndaQua.sch]
2021-01-26 add voltageGenerator to PCB
    [Sensor.sch, voltageregulator.sch]
2021-01-26 PDF and DWG files for robot diagrams
    [Diagrama Robo.dwg]
2021-01-26 Fixed .sch errors
    [fsm.sch]
2021-01-27 GerOndQuad updated
    [gerOndaQua.sch, gerOndaQua_1_0.sch]
2021-01-27 Sensor PCB corrected
    [Sensor.sch, Sensor_1_0.sch]
2021-01-27 Sensor and GeraOndQuad finished
    [Sensor.sch]
2021-01-27 PCB done
    [fsm.sch]
2021-01-27 Added final fsm_pcb version
    [fsm.sch]
2021-01-27 Added tmp version of pcb_debounce
    [debounce.sch]
2021-01-27 Updated Mechanical Diagrams
    Almost complete, while viewing in pdf lines appear grey because they're too thin, this issue will get resolved later
    [Diagrama Robo v2.dwg]
2021-01-27 Added push-button logic & layout
    [botao.sch]
2021-01-27 PTA Q PRREU
    [botao.sch, debounce.sch, fsm_LB.sch]
2021-01-28 Added fsm_LB
    [debounce.sch, fsm_LB.sch]
2021-01-28 added Kickad sensor
    [Sensor.kicad_pcb, Sensor.sch]
2021-01-28 Added final version fsm_LB
    [fsm_LB.sch]
2021-01-28 print simultions
2021-01-28 Diagram Updated and 3D Model Started
    Do not open the pdf file with Adobe Acrobat Reader to take prints, use other pdf viewer (chrome works for me) where lines don't appear grey. STL file is a 3D file format.
    [Diagrama Robo v2.dwg, Model Robo v2.stl]
2021-01-28 Corrected a small organization mistake
    [Diagrama Robo v2.dwg]
2021-01-28 motor control simulation completed
2021-01-28 added KiCad files
    [PC.kicad_pcb, PC.sch]
2021-01-29 KiCad final
    [PC.sch, fsm.kicad_pcb, fsm.sch]
2021-01-29 Pega bruno
    [fsm.kicad_pcb]
2021-01-29 Kicad projects finished
    [GeraOndQuad.kicad_pcb, GeraOndQuad.sch, Sensor.kicad_pcb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]
2021-01-29 Added fsm_LB_v1 & v2
    [fsm_LB.sch, fsm_v2.sch]
2021-01-29 Renamed fsm_LB/
    [fsm_LB.sch]
2021-01-29 corrected kiCad errors
    [GeraOndQuad.kicad_pcb, GeraOndQuad.sch, Sensor.kicad_pcb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]
2021-01-29 KiCad over
    [fsm.kicad_pcb, fsm.sch]
2021-01-29 Kicad GeraOndQuad update
    [GeraOndQuad.kicad_pcb]
2021-01-29 simulations and PCB
2021-01-29 Renamed some files and deleted trash
    [fsm.sch, fsm_LB.sch]
2021-01-30 GeraOndQuad Kicad name update
    [GeraOndQuad.kicad_pcb]
2021-01-30 update colors PADS and name in Kicad
    [GeraOndQuad.kicad_pcb, gerOndaQua.sch]
2021-01-30 update sensor pads and Kicad
    [Sensor.kicad_pcb, Sensor.sch]
2021-01-30 PCB prints finished
2021-01-30 Relatório final review
    [FSM_v1.8.xlsx]
2021-02-01 resitor value
    [Sensor.sch, gerOndaQua.sch]
2021-02-01 alteration in 3D view
    [fsm.kicad_pcb]
2021-02-01 Added missing dimensions and corrected some errors
    [Diagrama Robo v2.dwg]
2021-02-01 Improved pdf output
    [Diagrama Robo v2.dwg]
2021-02-01 edit resistor value
    [gerOndaQua.sch]
2021-02-01 state machine PCB
2021-02-01 PCB 3D
2021-02-01 added pcb prints
    [fsm_v2.sch]
2021-02-01 Renamed some files
    [Material(Preco).xlsx]
2021-02-02 melhorias ao circuito nao concluidas
2021-02-03 Changed OR type on sch
    [fsm_v2.sch]
2021-02-08 refresh images
    [Diagrama Robo v2.dwg, Diagrama_Robo_v2.dwg]
2021-02-08 tudo junto. Falta o que e para ser feito em conjunto
2021-02-08 edited simulations (output/input names)
    [Sensor.kicad_pcb, Sensor.sch, gerOndaQua.sch]
2021-02-08 add simulation print
2021-02-09 debounce images
    [DiagramaGantt.xlsx]
2021-02-11 add apresentation
    [DiagramaGantt.xlsx, ListaMaterial_appt.xlsx]
2021-02-11 apresentacao feita: - divisao de tarefas
2021-02-26 Final commit
    [DiagramaGantt.xlsx, ListaMaterial_appt.xlsx]
